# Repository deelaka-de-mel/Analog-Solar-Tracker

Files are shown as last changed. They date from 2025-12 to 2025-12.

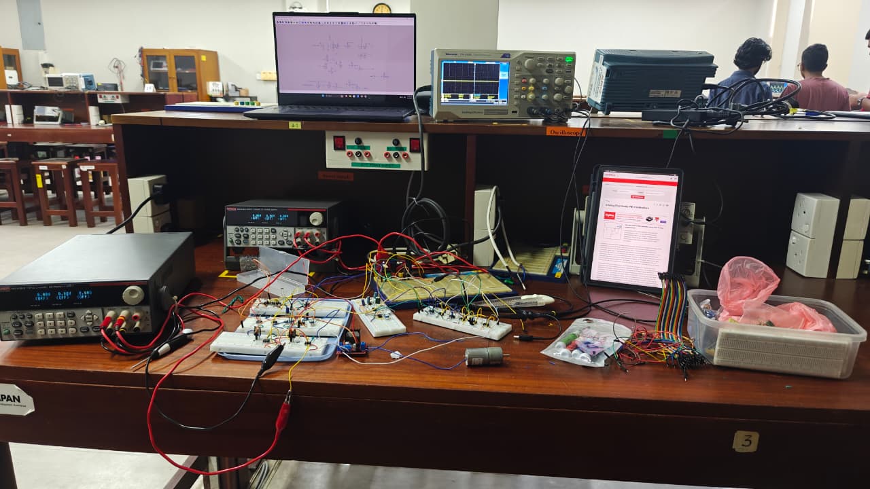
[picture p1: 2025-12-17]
Simulation and hardware testing/Hardware testing.jpg

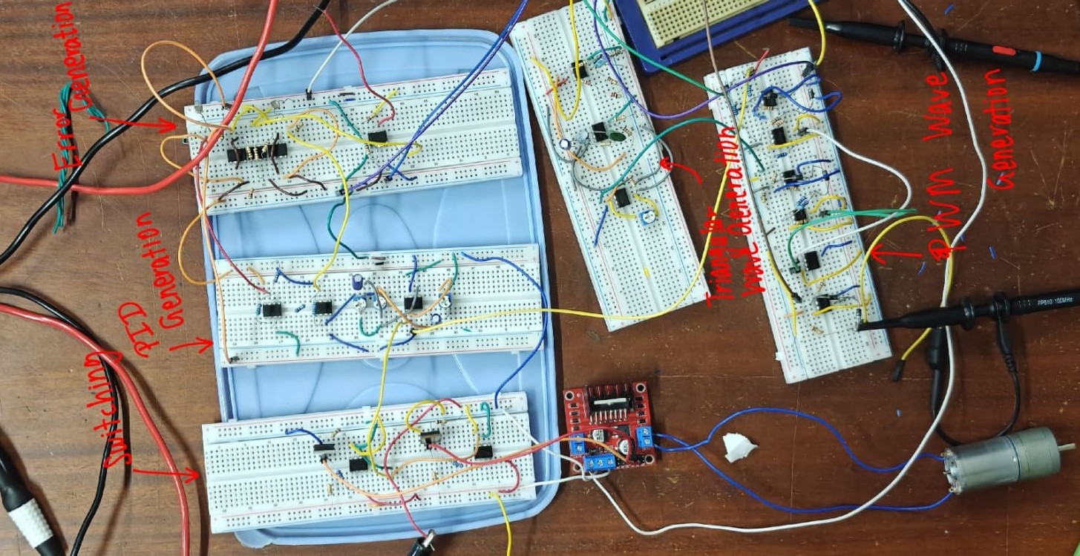
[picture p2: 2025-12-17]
Simulation and hardware testing/breadboard .jpg

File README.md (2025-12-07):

# Analog-Solar-Tracker
Design and implementation of a single-axis automatic solar tracker aimed at maximizing
photovoltaic energy generation using optimized panel orientation. Due to maximum electrical
output of a solar panel depending heavily on the angle of incidence and intensity of sunlight,
a dynamic tracking system is required to maintain high efficiency under varying environmen-
tal conditions. This system fully employs a purely analog PID control circuit, made using
OPAMPs and discrete electronic components to continuously observe the sunlight and change
the direction and rotate the solar panel accordingly. All circuitry was simulated using LT-
Spice and subsequently validated using breadboard testing as well. A complete PCB design
was done using Altium Designer following JLCPCB’s manufacturing guidelines, and me-
chanical integration is done using 3D printing using models done on SOLIDWORKS. The
final implementation demonstrates a reliable and responsive analog system for enhanced solar
energy harvesting.

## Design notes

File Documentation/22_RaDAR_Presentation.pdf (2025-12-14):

## RaDAR

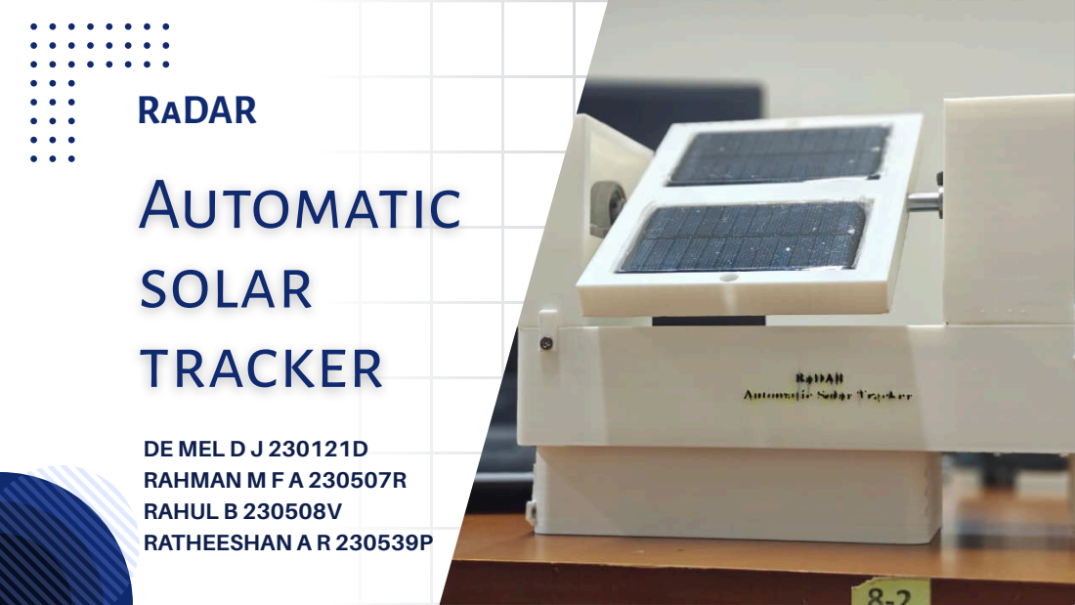
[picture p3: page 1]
RAHMAN M F A 230507R RAHUL B 230508V RATHEESHAN A R 230539P

Automatic
solar
tracker

DE MEL D J 230121D

# Introduction & Overview

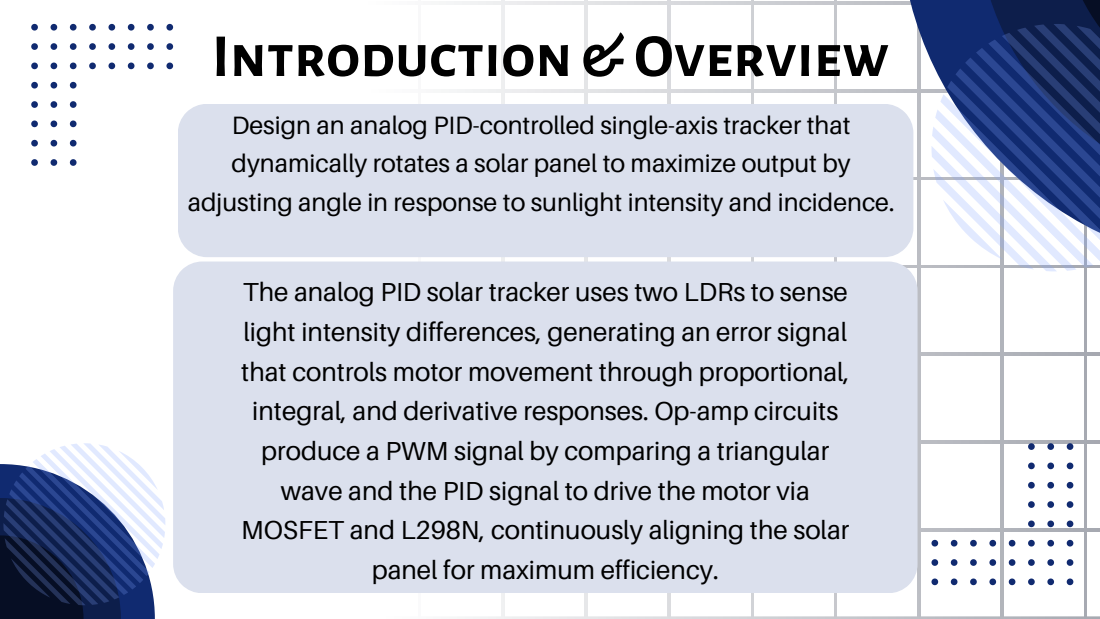
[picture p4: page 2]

Design an analog PID-controlled single-axis tracker that dynamically rotates a solar panel to maximize output by

adjusting angle in response to sunlight intensity and incidence.

The analog PID solar tracker uses two LDRs to sense light intensity differences, generating an error signal

that controls motor movement through proportional, | integral, and derivative responses. Op-amp circuits

MOSFET and L298N, continuously aligning the solar | produce a PWM signal by comparing a triangular wave and the PID signal to drive the motor via

panel for maximum efficiency.

# BlockDiagram

## Error

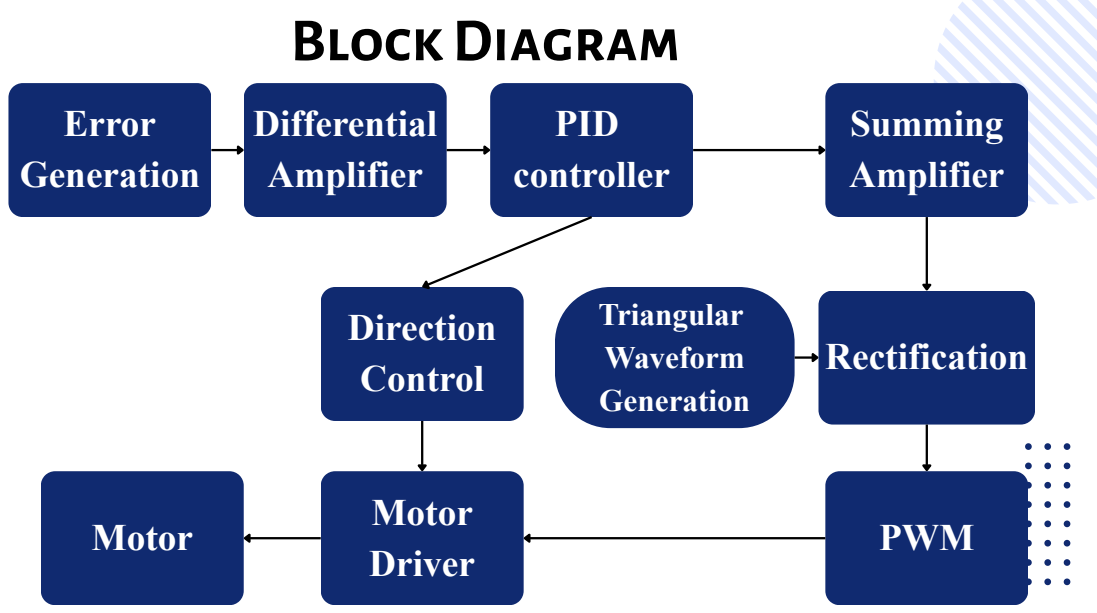
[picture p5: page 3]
Triangular Waveform Generation; Generation; Differential Amplifier; PID controller; Summing Amplifier; Rectification; PWM; Motor Driver; Motor; Direction Control

SystemOverview,

# specifications

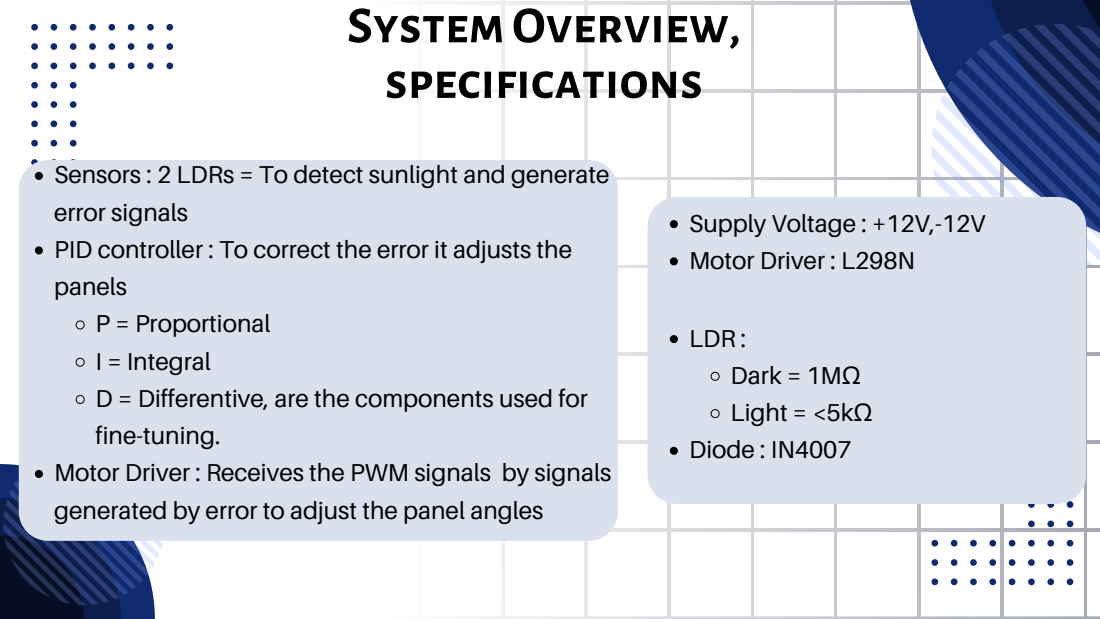
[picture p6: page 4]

Sensors : 2 LDRs = To detect sunlight and generate
error signals PID controller : To correct the error it adjusts the

Supply Voltage : +12V,-12V Motor Driver : L298N

panels | P = Proportional | | LDR :

I = Integral D = Differentive, are the components used for fine-tuning. | | Dark = 1MΩ Light = <5kΩ

Motor Driver : Receives the PWM signals generated by error to adjust the panel angles | | by signals | Diode : IN4007

SystemOverview,

# specifications

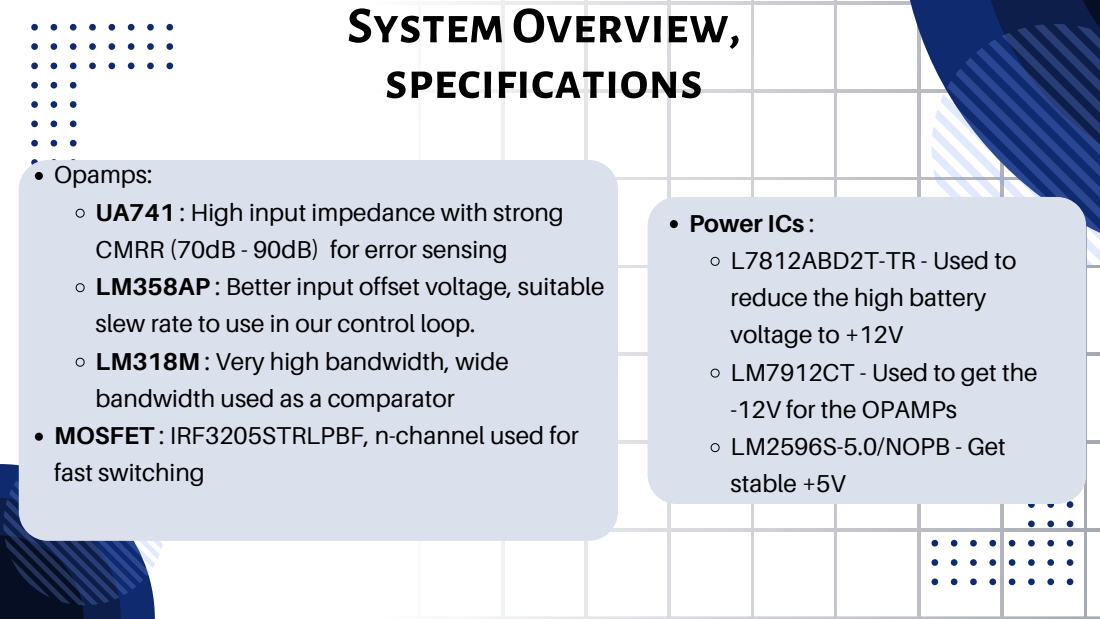
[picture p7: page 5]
Opamps:; LM2596S-5.0/NOPB - Get

UA741 : High input impedance with strong CMRR (70dB - 90dB) for error sensing

Power ICs : L7812ABD2T-TR - Used to

LM358AP : Better input offset voltage, suitable slew rate to use in our control loop. | reduce the high battery voltage to +12V

MOSFET : IRF3205STRLPBF, n-channel used for | LM318M : Very high bandwidth, wide bandwidth used as a comparator | LM7912CT - Used to get the -12V for the OPAMPs

fast switching | | stable +5V

# PCB schematic

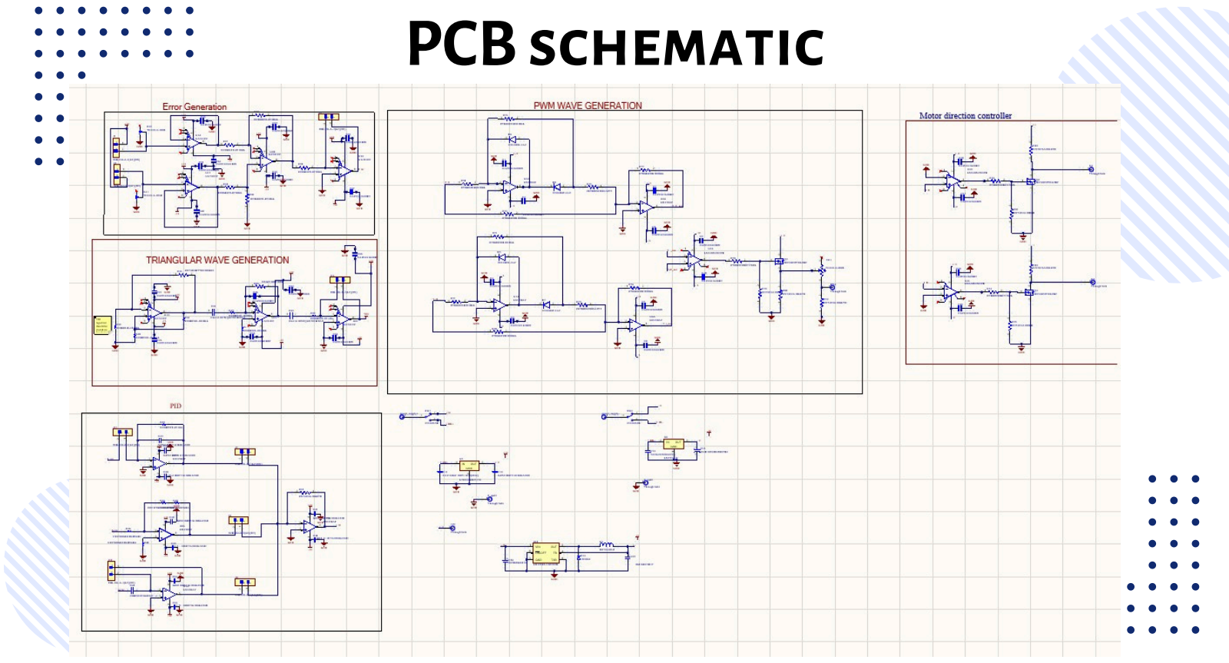
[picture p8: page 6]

# PCB 2Dview

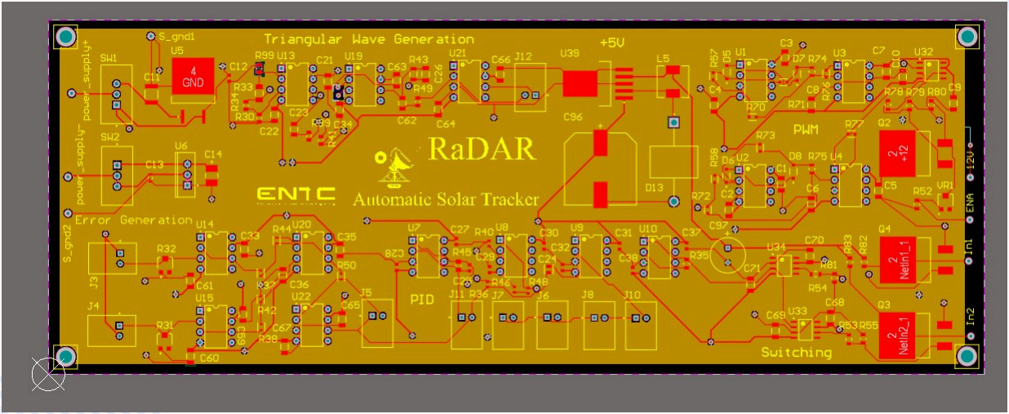
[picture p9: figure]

# PCB

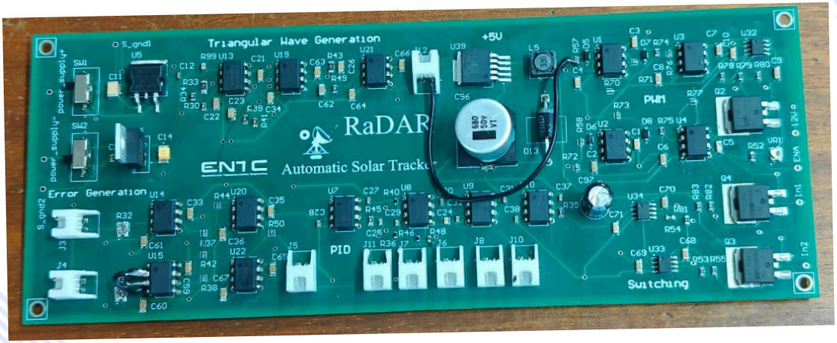
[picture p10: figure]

# Enclosure

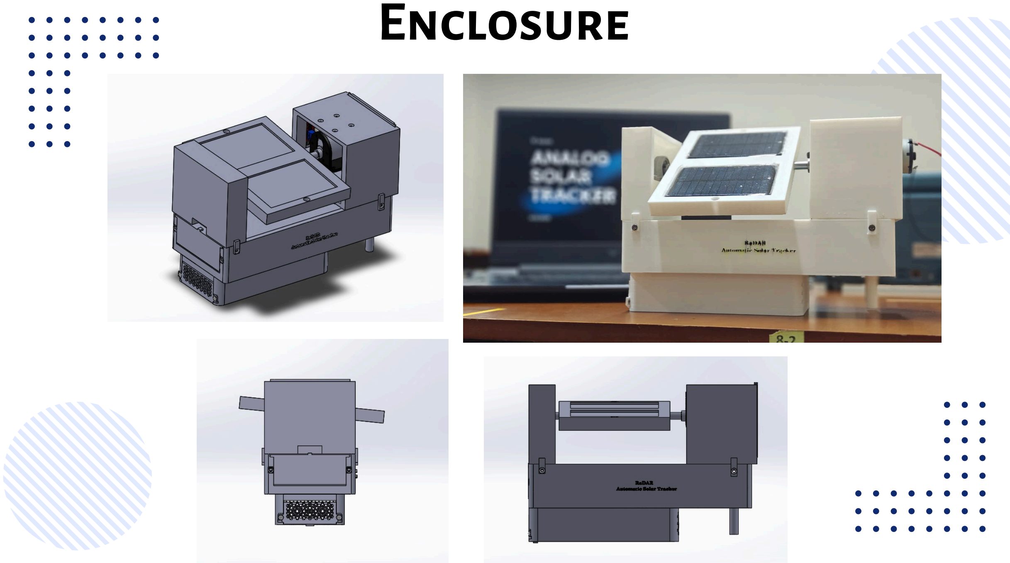
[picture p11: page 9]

# Initial Test

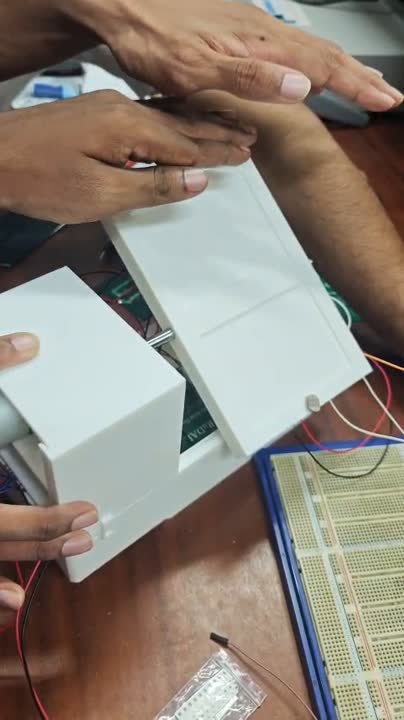
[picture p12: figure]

# Final Testing

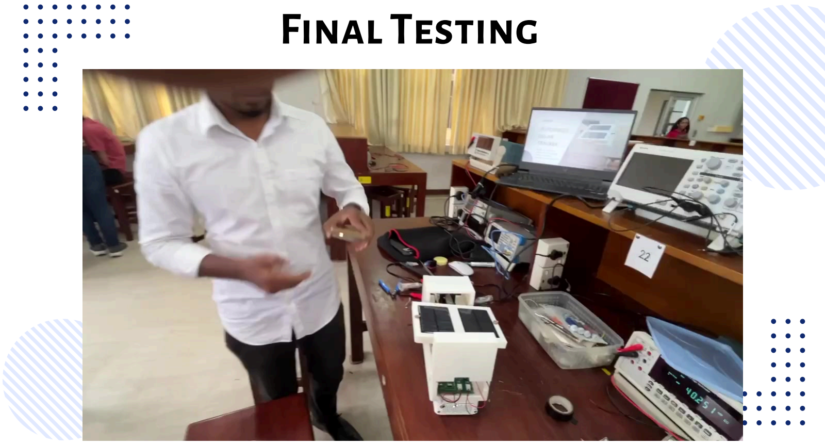
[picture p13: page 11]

# Future Improvements

Integrate a dual-axis tracking system to improve precision.

### Include real-time data logging of panel position, sunlight intensity, and power output. Add low-power standby mode

and automatic night reset to reduce power consumption.

### Design a weather-proof enclosure for outdoor deployment

and long-term stability.

Name | Tasks
Deelaka | Circuit Design, Software simulation, Soldering
Abdul Rahman | Enclosure using SOLIDWORKS, Soldering
Rahul | Circuit Designing, Testing, Soldering
Rakesh | PCB Designing, Assembling, Soldering

# Task Allocation

# Thank you

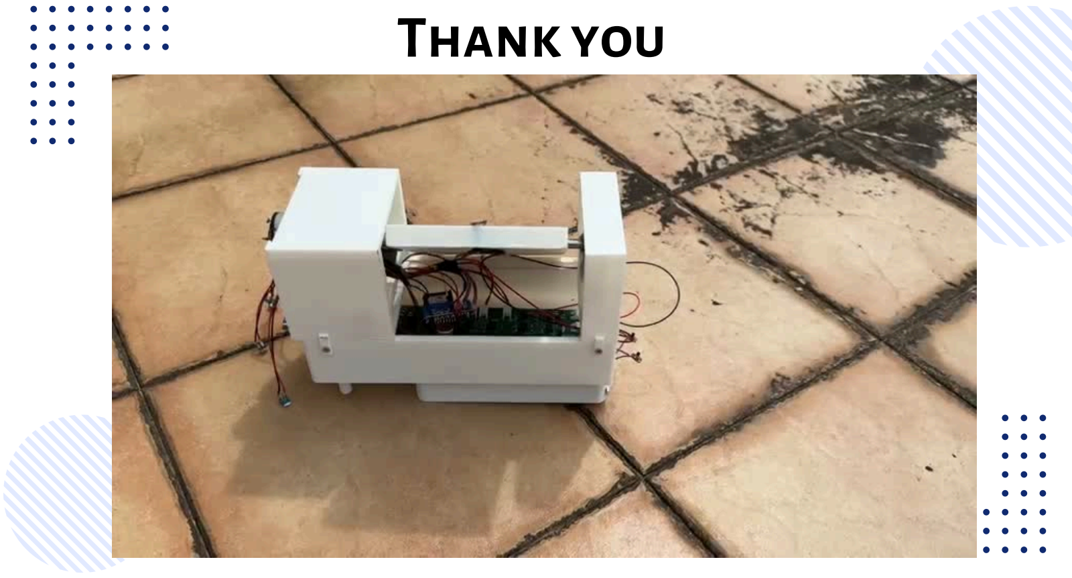
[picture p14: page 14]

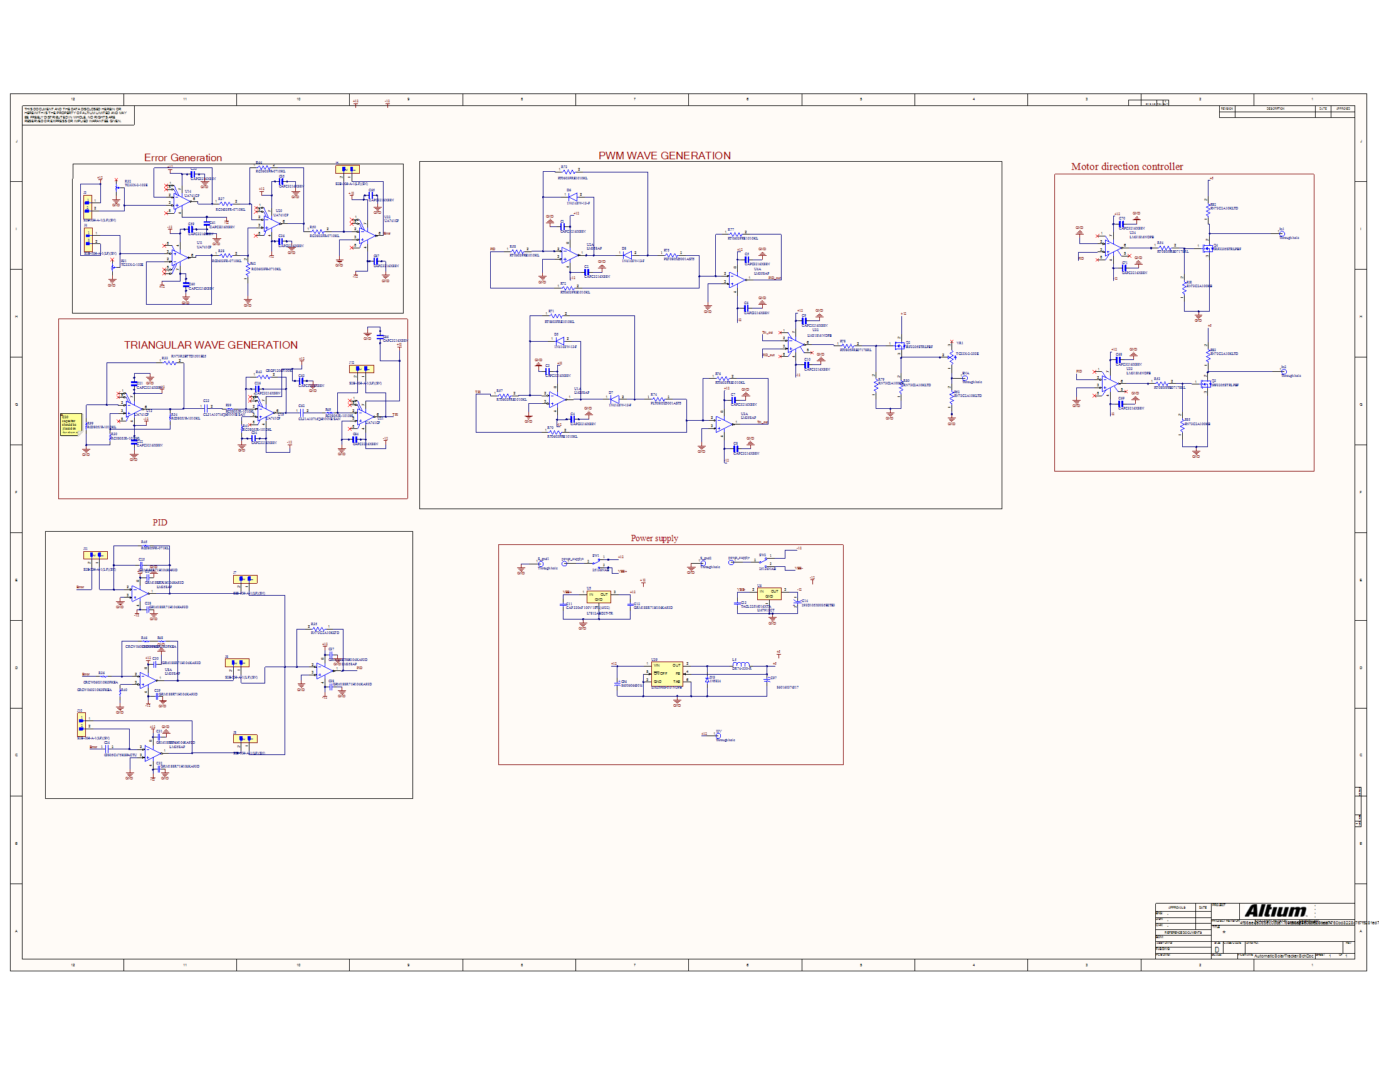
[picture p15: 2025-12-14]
22_RaDAR_EN2091_Altium_files/AutomaticSolarTracker.png

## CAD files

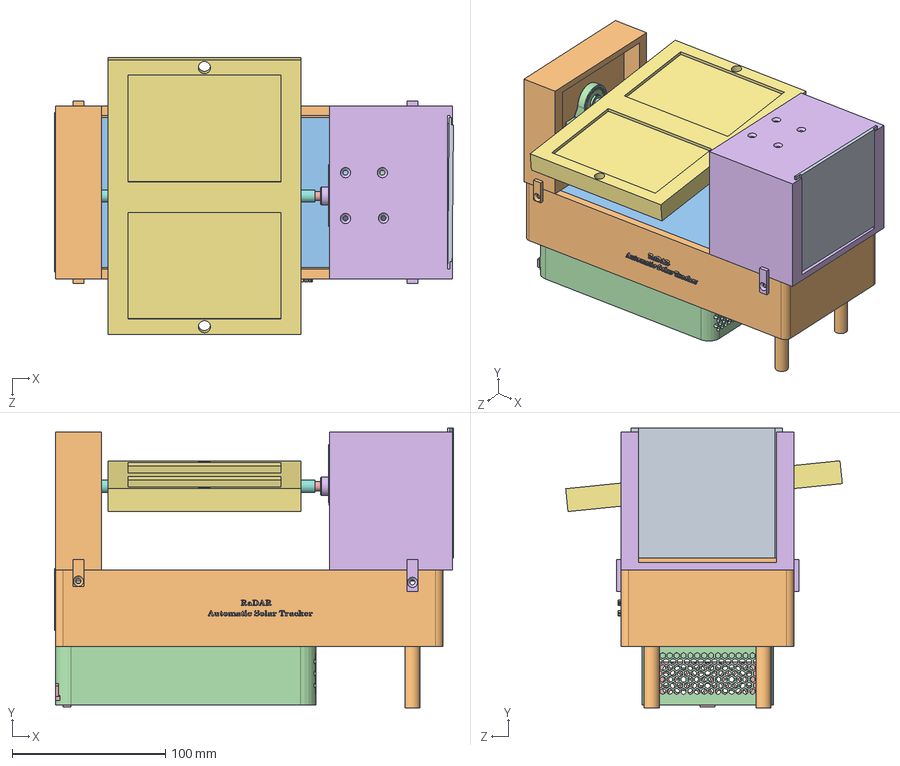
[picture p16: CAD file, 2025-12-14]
22_RaDAR_EN2091_Solidworks_files/Final_Assembly.SLDASM
260.4 x 182.7 x 180.6 mm
Base_final
Base_f_lid
Battery Base
Battery_lower_base
Gear
Solar_panel
shaft
Gear_opener
stand
GEARED BODY, MOTOR, JGB37-520
DC MOTOR, JGB37-520
MOTOR SHAFT, JGB37-520
SHAFT COUPLER, JGB37-520
COUPLING BRACKET, GEARED BODY TO DC MOTOR, JGB37-520
PLASTIC COVER, DC MOTOR, JGB37-520
CONNECTION, DC MOTOR, JGB37-520 x 2
pan cross head_am x 3
L298N Motor Driver.step
JGB37-520 12 v metal geared motor bracket
Power Screw Bearing Part - KP08 SUPPORT BEARING-Edited.step

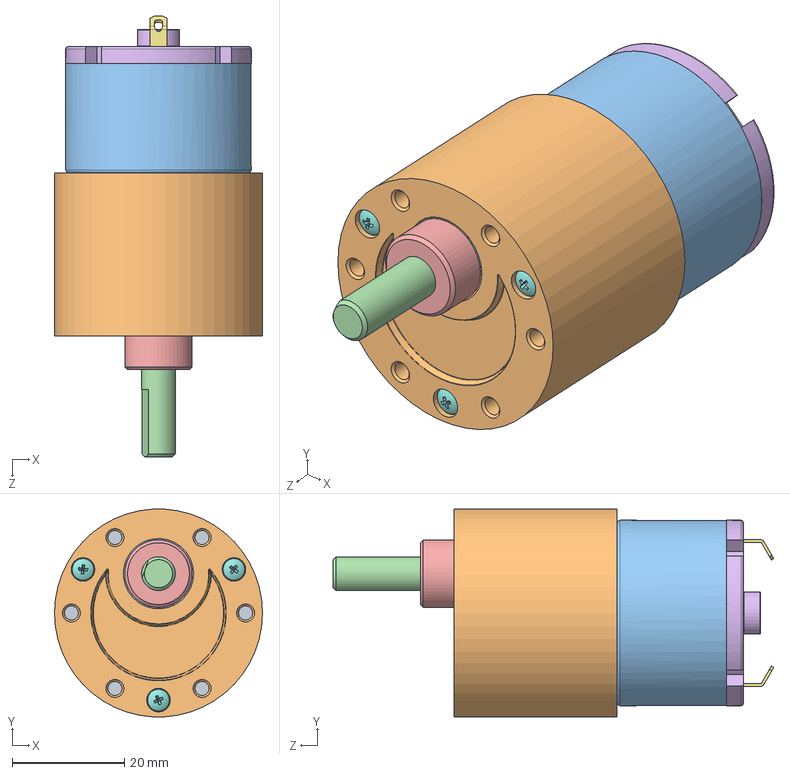
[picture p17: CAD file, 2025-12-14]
22_RaDAR_EN2091_Solidworks_files/JGB37-520.SLDASM
37.0 x 36.9 x 78.4 mm
GEARED BODY, MOTOR, JGB37-520
DC MOTOR, JGB37-520
MOTOR SHAFT, JGB37-520
SHAFT COUPLER, JGB37-520
COUPLING BRACKET, GEARED BODY TO DC MOTOR, JGB37-520
PLASTIC COVER, DC MOTOR, JGB37-520
CONNECTION, DC MOTOR, JGB37-520 x 2
pan cross head_am x 3

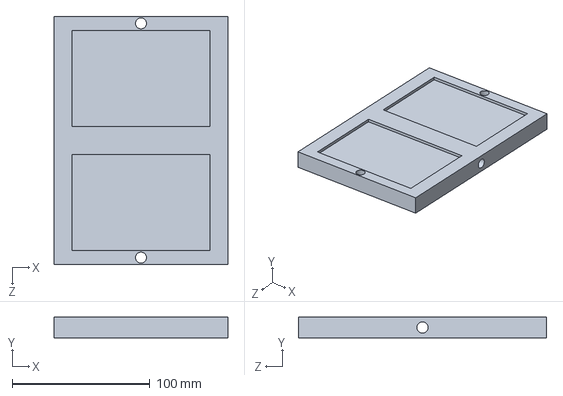
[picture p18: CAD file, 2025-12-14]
22_RaDAR_EN2091_Solidworks_files/Solar_panel.SLDPRT
126.0 x 15.0 x 180.0 mm

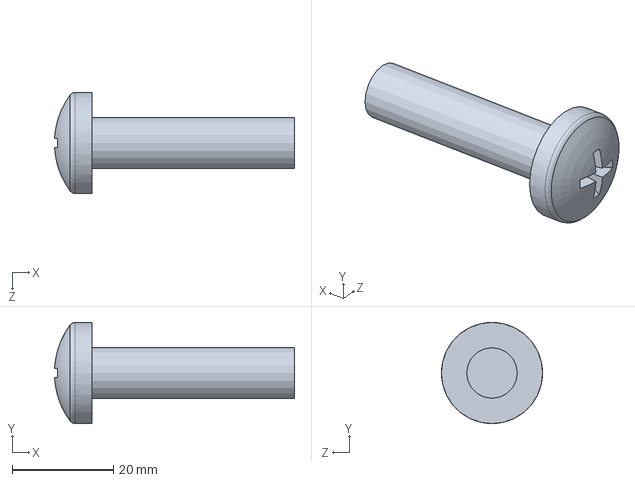
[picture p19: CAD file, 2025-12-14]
22_RaDAR_EN2091_Solidworks_files/pan cross head_am.sldprt
47.4 x 20.0 x 20.0 mm

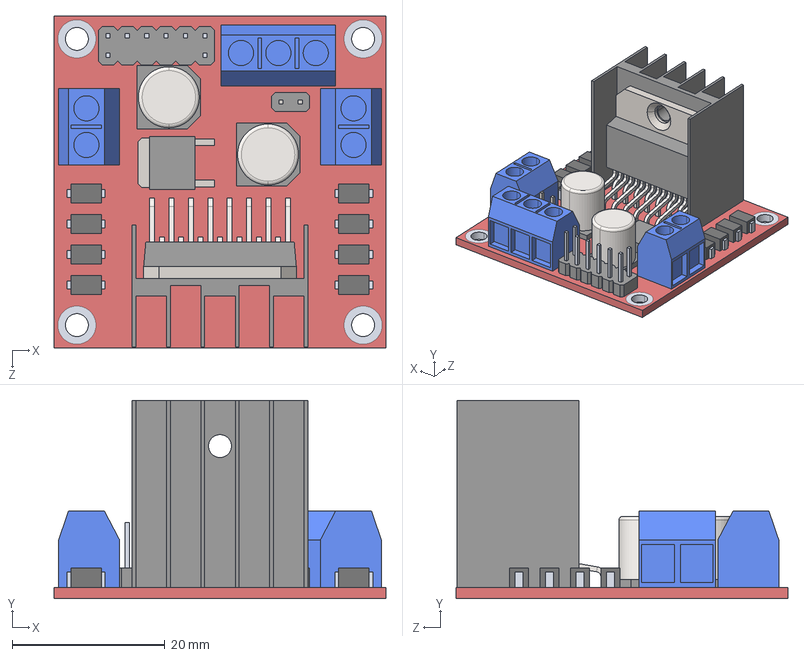
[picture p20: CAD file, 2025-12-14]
22_RaDAR_EN2091_Solidworks_files/L298N Motor Driver.STEP
43.5 x 26.0 x 43.5 mm

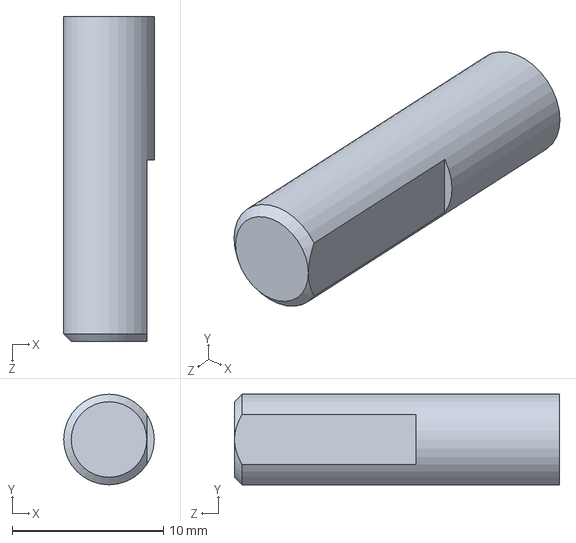
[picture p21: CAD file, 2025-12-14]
22_RaDAR_EN2091_Solidworks_files/MOTOR SHAFT, JGB37-520.SLDPRT
6.00 x 6.00 x 21.5 mm

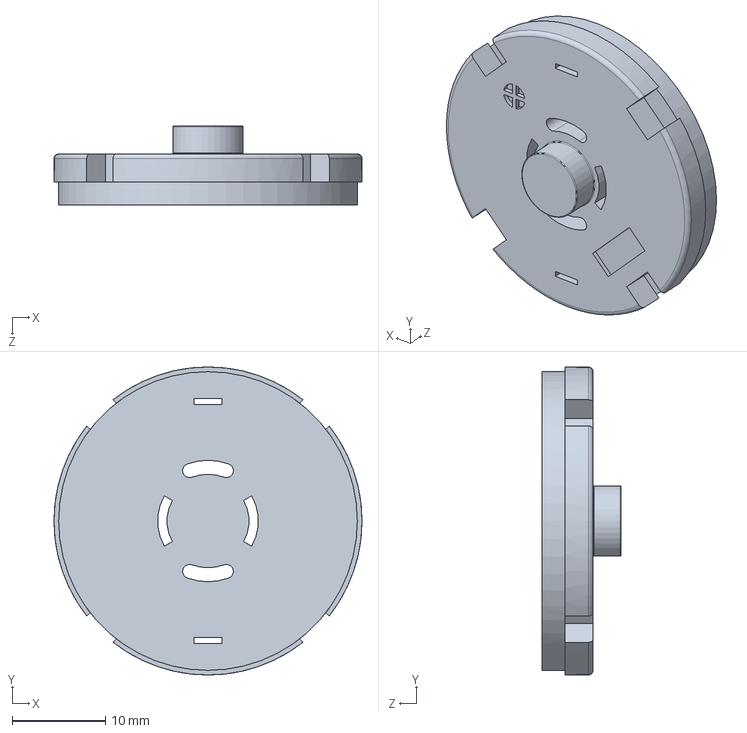
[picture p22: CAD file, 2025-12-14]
22_RaDAR_EN2091_Solidworks_files/PLASTIC COVER, DC MOTOR, JGB37-520.SLDPRT
33.0 x 33.0 x 8.50 mm

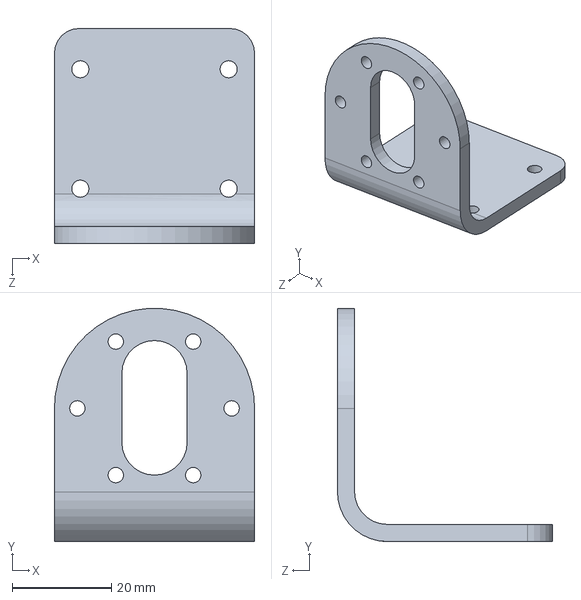
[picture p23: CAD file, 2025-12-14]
22_RaDAR_EN2091_Solidworks_files/JGB37-520 12 v metal geared motor bracket.SLDPRT
40.3 x 47.0 x 43.3 mm

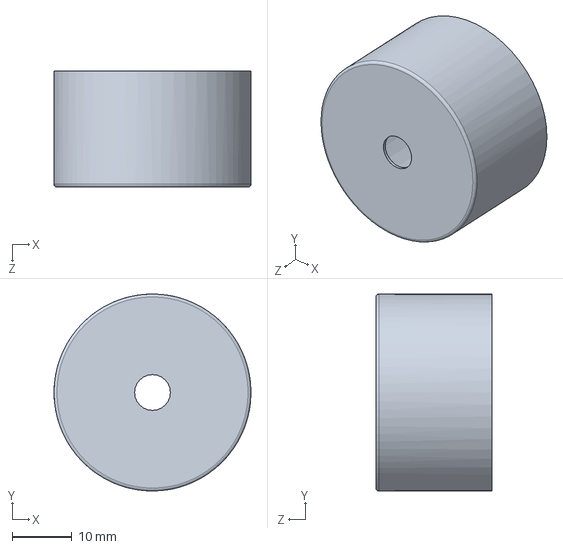
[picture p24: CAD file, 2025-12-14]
22_RaDAR_EN2091_Solidworks_files/DC MOTOR, JGB37-520.SLDPRT
33.0 x 33.0 x 19.5 mm

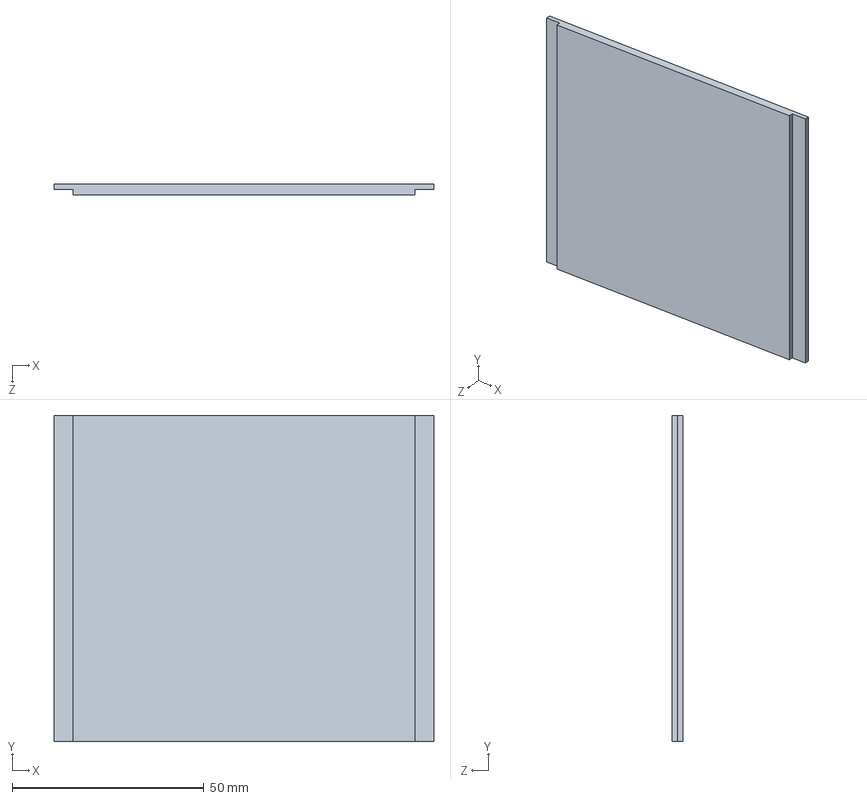
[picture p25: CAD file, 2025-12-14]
22_RaDAR_EN2091_Solidworks_files/Gear_opener.SLDPRT
99.0 x 85.0 x 2.90 mm

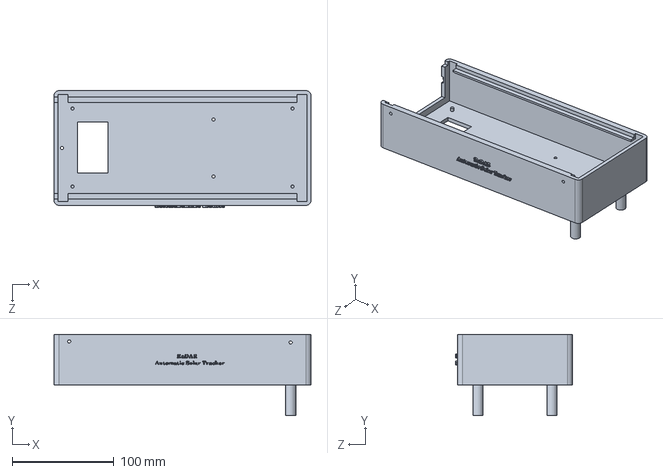
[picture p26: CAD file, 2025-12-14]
22_RaDAR_EN2091_Solidworks_files/Base_final.SLDPRT
253.0 x 80.0 x 115.0 mm

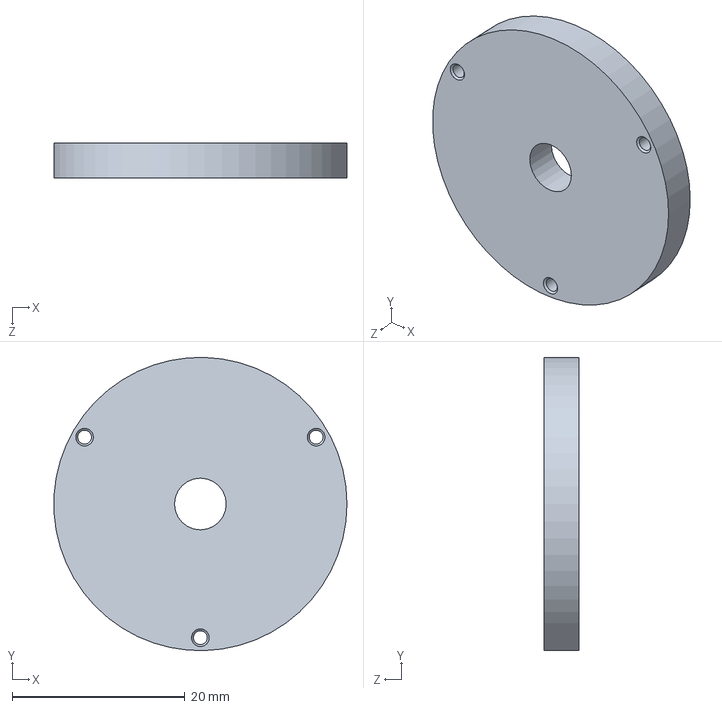
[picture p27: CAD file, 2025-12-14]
22_RaDAR_EN2091_Solidworks_files/COUPLING BRACKET, GEARED BODY TO DC MOTOR, JGB37-520.SLDPRT
34.0 x 34.0 x 4.00 mm

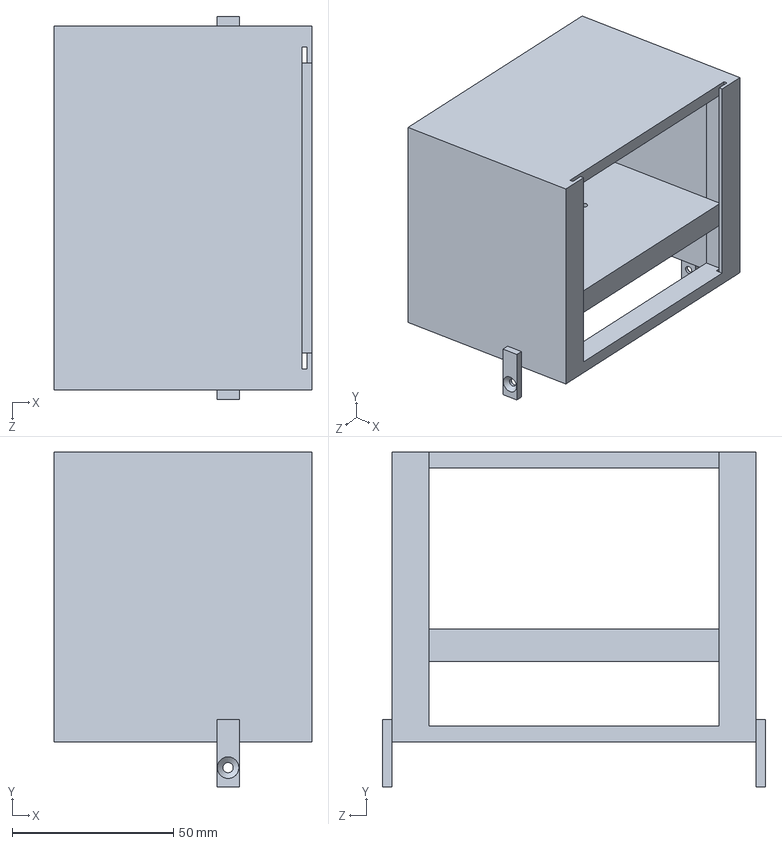
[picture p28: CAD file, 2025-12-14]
22_RaDAR_EN2091_Solidworks_files/Gear.SLDPRT
80.0 x 104.0 x 119.0 mm

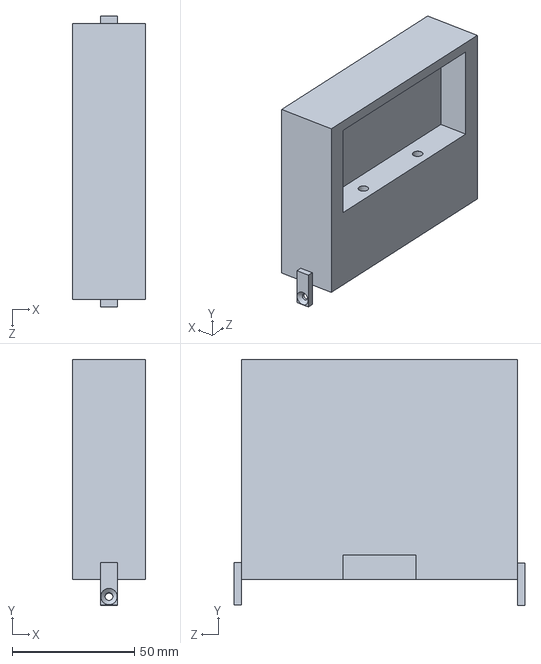
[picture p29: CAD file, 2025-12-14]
22_RaDAR_EN2091_Solidworks_files/stand.SLDPRT
30.0 x 100.8 x 119.0 mm

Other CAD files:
22_RaDAR_EN2091_Solidworks_files/GEARED BODY, MOTOR, JGB37-520.SLDPRT
22_RaDAR_EN2091_Solidworks_files/shaft.SLDPRT
22_RaDAR_EN2091_Solidworks_files/L298N Motor Driver.step.SLDPRT
22_RaDAR_EN2091_Solidworks_files/SHAFT COUPLER, JGB37-520.SLDPRT
22_RaDAR_EN2091_Solidworks_files/Base_f_lid.SLDPRT
22_RaDAR_EN2091_Solidworks_files/Battery Base.SLDPRT
22_RaDAR_EN2091_Solidworks_files/Battery_lower_base.SLDPRT
22_RaDAR_EN2091_Solidworks_files/CONNECTION, DC MOTOR, JGB37-520.SLDPRT
22_RaDAR_EN2091_Solidworks_files/Power Screw Bearing Part - KP08 SUPPORT BEARING-Edited.step.SLDPRT

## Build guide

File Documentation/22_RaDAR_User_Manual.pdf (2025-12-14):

# User Manual Analog Automatic Solar Tracker

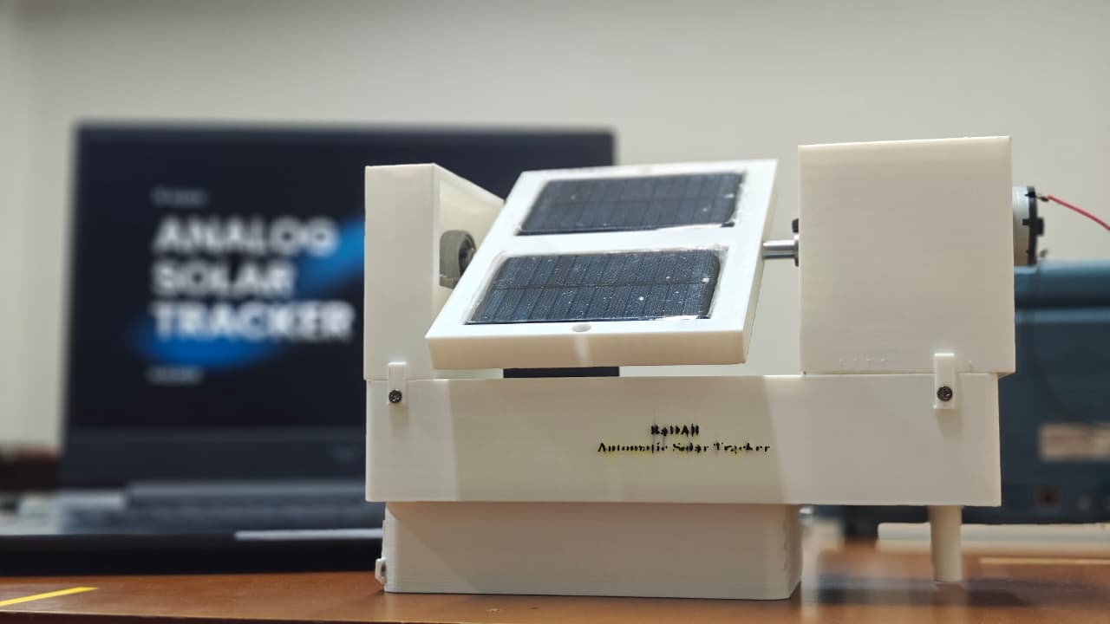
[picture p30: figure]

Automatic Solar Tracker | RaDAR

## 1 Introduction

This User Manual provides installation, operation, calibration, and maintenance instructions for the Analog Automatic Solar Tracker. The system is a fully analog, single-axis solar tracking platform designed to orient photovoltaic panels toward maximum solar irradiance using differential light sensing and analog control circuitry.

## 2 Package Contents

The following items are included with the Analog Automatic Solar Tracker:

- Fully assembled tracker enclosure with internal analog control PCB
- Integrated battery pack consisting of eight 3.7 V, 1000 mAh Li-ion cells
- DC geared motor (12 V, 50 rpm) pre-mounted to the mechanical structure
- Dual LDR sensors embedded on both sides of the solar panel
- Two additional spare LDR sensors
- Mechanical mounting brackets (pre-installed)
- User Manual

Note: No external power adapter is supplied. Batteries are user-replaceable via the battery enclosure.

## 3 Safety Information

- Maximum Input Voltage: The system must not be operated beyond +35 V and –35 V under any circumstances, as this may cause permanent damage to the analog circuitry.
- Reverse Polarity: The tracker does not include reverse polarity protection. Ensure correct battery orientation before powering the system.
- Motor Operation: Risk of motor overheating is minimal, as the DC motor operates only intermittently during solar tracking and remains idle once alignment is achieved.
- Short-Circuit Risk: Short circuits may occur if the system is exposed to rain or moisture. The tracker is not designed for wet or outdoor environments.
- Environmental Exposure: Do not operate the system in rainy conditions or high-humidity environments without proper enclosure sealing.
- Maintenance Safety: Always switch OFF the power using the DPDT switch before handling internal components or replacing batteries.

## 4 Mechanical Installation

The solar tracker can be installed on a table-top, rooftop, or ground-mounted surface where direct sunlight is available.

1. Secure the tracker base to a stable surface using M3 bolts.
2. Mount the solar panel firmly onto the rotating bracket.
3. Ensure that no mechanical obstruction restricts the panel movement.
4. Verify that the panel rotation is limited to approximately ±45◦

to ±60◦ as designed.

1

Automatic Solar Tracker | | RaDAR

## 5 Electrical Connections

1. The system is powered by eight 3.7 V Li-ion batteries configured to provide +12 V, –12 V, and ground rails.
2. Power is controlled using the DPDT switch connected to the battery holders.
3. The DC motor is driven directly from the control PCB via an L298N motor driver.
4. LDR sensors are wired directly to the PCB through dedicated sensor inputs.

Note: No external fuse is used in the current design.

## 6 Operation

Once powered ON using the DPDT switch, the solar tracker begins automatic operation. The system continuously compares light intensity detected by the LDR sensors and rotates the panel accordingly.
The tracker initially hunts for the direction of maximum light intensity and gradually stabi-lizes. Once the incident sunlight becomes approximately perpendicular to the panel surface, the motor stops automatically. An onboard indicator LED on the L298N motor driver provides basic operational feedback.

## 7 Calibration Procedure

Calibration is required only once during initial setup.

1. Place the tracker under uniform sunlight or ambient lighting.
2. Adjust the fixed potentiometers on the PCB to balance both LDR sensor outputs.
3. Shade one LDR sensor slightly and observe motor response.
4. Fine-tune gain adjustment potentiometers until smooth and stable tracking is achieved.

## 8 Maintenance

Routine maintenance requirements are minimal.

- Clean the LDR sensors if dust, dirt, or rain residue accumulates.
- Inspect the mechanical structure periodically for loosened bolts.
- Battery replacement should be performed when tracking response becomes sluggish.

## 9 Troubleshooting

Issue | Possible Cause | Corrective Action
Motor does not rotate | Battery depleted or switch OFF | Recharge or replace batteries, check switch
Panel moves in wrong direction | LDR polarity mismatch | Swap LDR connections or recalibrate
Continuous oscillation | Excessive gain setting | Reduce gain using potentiometer
No stabilization | Unequal sensor exposure | Re-align LDR placement

2
